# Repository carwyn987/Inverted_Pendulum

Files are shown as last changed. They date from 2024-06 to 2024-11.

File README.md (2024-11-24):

# Inverted-Pendulum Project

## What is an inverted pendulum?
An [inverted pendulum](https://en.wikipedia.org/wiki/Inverted_pendulum) is a dynamic system with the center of mass above its pivot point, generally constrained to one rotational degree of freedom. While a pendulum is stable, inverting a pendulum requires active balancing applied to it. Generally, this is performed by applying torque to the pendulum directly, or shifting the base longitudinally.

## History of Project

### Final TD3 Performance

https://github.com/user-attachments/assets/6cc0a676-86f2-4fd9-accb-2f986fe4a135

### Postsite / Retrospective Analysis

Reinforcement learning is ***INCREDIBLY CHALLENGING*** to transfer from simulation to reality - especially if you don't know the dynamics of the environment. 

The biggest difficulty was matching my simulation to the environment:
 - Most inverted pendulum simulations (CartPole-v1 from gymnasium) have force as the input quantity. My hardware used a stepper motor, with discrete choices for step sizes and timing. 
 - Due to the stepper motor, I also was constrained to a maximum speed.
 - The default parameters for the gymnasium environment do not seem to map to true dynamics. It seemed like my pendulum fell much faster than the simulation  rod.
 - Traditional methods such as PID control loops are well known for a reason - they work, are simple to set up. The only annoyance is tuning.

### Presite Updates

DQN Model balances pendulum, but cannot converge from hanging (stable) initialization in a reasonable amount of time and resources.

TD3 trained to convergence on episodes of length 1000 steps (0.02s resolution = 20s). Video below. Note: there are perturbations in the test, which explain some unexpected movements. These represent external forces acting on the pole, or noise in the system.

https://github.com/carwyn987/Inverted_Pendulum/assets/28845732/e16f0db4-fafe-4622-8498-058ad09bbe2e

Reward function that worked well for TD3:
```
reward = math.cos(theta % (2*math.pi)) + 1
if theta > -1 * math.pi/24 and theta < math.pi/24:
    reward += 10
if reward < 0: reward = 0
```
Note the lack of an explicit x-position component, which explains the full use of horizontal space by the agent.

### 2024

After a long intermission, I have decided to re-approach the project. However, I have an agenda in mind. As I will be traveling back to where the hardware is for one week only, I wish to simulate a solutions type of job, where the employee is dispatched to an on-site location, where they are responsible for quickly getting a system up and running. Therefore, I plan to prepare for this trip, and see how much I can minimize the on-site time necessary to get the pendulum balanced. Furthermore, I want to make the goals specific and as numerous as possible, so the goal is the following:

1. Enable the pendulum to balance "continuously". For testing purposes, I define this as "achieved" when the following test are completed successfully:
   - 5 individual tests, all 5 must pass first try with a unique codebase.
   - Sample an initial pendulum angle from vertical within the range of [-10,10] degrees.
   - Sample an initial longitudinal position within the middle 30% of the total range.
   - Set up the initial conditions by hand, and release contact with the pole as soon as movement is perceived after starting the program.
   - The pole must balance for 60 seconds for "success" to be achieved.
2. The same algorithm should enable the pole to swing up from a stationary position. I define this as "achieved" when the following test are completed successfully:
   - Begin with the pendulum stationary hanging at the lowest point (180 degrees from vertically upward (azimuth/heading/yaw(?)))
   - Execute the program, and without any contact from the tester, the pendulum should reach a balanced (varying <10 degrees from vertical over at least 10 seconds) within 30 seconds.
3. Just for funsies, a separate algorithm should enable the pendulum to make rotations of the pendulum. I define this as "achieved" when the following test are completed successfully:
   - Starting the test with the rod stationary in the downwards position, the rod should make >=10 full rotations in under 45 seconds.
4. Reach goal: if I achieve this, consider me a god (lowercase g). Modify the system somehow (make it visually based perhaps?) to enable a double pendulum to balance. This will involve hardware modifications to add another joint.

### 2018

In the naive implementation (2018), a deterministic model was created as a decision tree, with a few possible movements based from binning various encoder angles. It was during this year when the hardware component was constructed, and the results were presented in an independent research project class.

Unfortunately, the feedback loop was not responsive enough to maintain a balanced state, however the proof of concept was there.

During this phase, a few iterations of design were explored. Primarily, testing was performed on both a Raspberry PI and an Arguino Mega. There were moments of significant garbage collection, which justified use of the Arduino. Furthermore, the initial design of the hardware used a drawer slide and a servo, which was not an ideal combo due to the control of the servo, and the significant mass of the drawer slide, which contributed to a system with minimal ability to impart movement to the pendulum.

https://github.com/carwyn987/Inverted_Pendulum/assets/28845732/88b4a921-044d-4a91-877d-22acfd15797b

https://github.com/carwyn987/Inverted_Pendulum/assets/28845732/74fb59c1-3fed-446d-82f0-261624505b5c

These can also be viewed on [my youtube channel](https://www.youtube.com/channel/UCNOUx60VSDCHhShPJUi3yFg).

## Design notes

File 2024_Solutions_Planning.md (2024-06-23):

# Overview

Here I will plan the technical aspects to ensure readiness and success for on-site integration and testing.

# Review of Goals from README

1. Enable the pendulum to balance "continuously". For testing purposes, I define this as "achieved" when the following test are completed successfully:
   - 5 individual tests, all 5 must pass first try with a unique codebase.
   - Sample an initial pendulum angle from vertical within the range of [-10,10] degrees.
   - Sample an initial longitudinal position within the middle 30% of the total range.
   - Set up the initial conditions by hand, and release contact with the pole as soon as movement is perceived after starting the program.
   - The pole must balance for 60 seconds for "success" to be achieved.
2. The same algorithm should enable the pole to swing up from a stationary position. I define this as "achieved" when the following test are completed successfully:
   - Begin with the pendulum stationary hanging at the lowest point (180 degrees from vertically upward (azimuth/heading/yaw(?)))
   - Execute the program, and without any contact from the tester, the pendulum should reach a balanced (varying <10 degrees from vertical over at least 10 seconds) within 30 seconds.
3. Just for funsies, a separate algorithm should enable the pendulum to make rotations of the pendulum. I define this as "achieved" when the following test are completed successfully:
   - Starting the test with the rod stationary in the downwards position, the rod should make >=10 full rotations in under 45 seconds.
4. Reach goal: if I achieve this, consider me a god (lowercase g). Modify the system somehow (make it visually based perhaps?) to enable a double pendulum to balance. This will involve hardware modifications to add another joint.

# Brainstorming

## Design Questions
 - Will I run compute on the same machine as the control? 
   - If I train on my laptop, it may be easier to use an ethernet communication interface, simply using the arduino as an intermediary.
 - How will I train? Is there a sample and time efficient enough algorithm to run in real-time, or is pretraining necessary?
 - If I simulate the environment, how will I ensure generalization to real life? 
   - Should I parameterize on intrinsic properties, such as mass of rod, total longitudinal distance, and maximum movement speeds
   - Will training on all of these parameters be prohibited on my local machine (3080ti)?
 - Simulation environment?
   - Python Gym (now gymnasium)
   - Gazebo (use ROS)?
   - Unreal Engine?
 - How should I format separation of training and inference? Presumably have a real-time inference program, potentially in a faster language such as C++.
   - This implies saving of model weights and loading in C++. Are there C++ libraries for this? (PyTorch C++ API)

## Predicted Issues

 - The encoder readings may not translate to the trained-upon data.
   - Compute a mapping function given some benchmark with an expectation (pendulum oscillations under gravity). Furthermore, it may be an interesting idea to use benchmarks like this as parameters (time for the pendulum to come to a stop given a 30 degree initialized unassisted swing (aka representation of system friction) - may differ if platform can and can't move).
 - The response of a given control signal will vary, in moments as well as duration, magnitude, and oscillatory behavior. 
   - Similar approach to encoder using a mapping. Perhaps also run some tests to see if we can replicate our trained-upon data?
 - Similar to my prior attempts, there will be an issue with the fact that I am currently dead-reckoning longitudinal position.

## Ideas

 - Redesign to use a camera for inputs
   - This will remove the need to use an encoder, and allow for determination of longitudinal displacement. Furthermore, it will allow me to try a double pendulum regardless of not having another encoder.
   - However, it will be challenging to ensure generalization. I may need to simulate the environment with a variety of backgrounds, and a particularly colored rod for this to work well. I could also use a colored sheet as the background, but that feels like cheating.
 - Set up a cloud-based GPU training device that can take an image of the environment. This will allow significant speed-ups due to larger batch sizes, and data and model parallelism capability. Therefore, it will be more realistic to retrain within an hour or two. That being said, in my experience, it's unlikely (if the code is not buggy) a task like this will require more than 24 hours of training, which is technically doable locally in the time frame allotted.
 - Modularize the system. Have a few interchangeable components for each module. An example of this would be having a module reponsible for determining the absolute angle of the pendulum. Then, I can build an image-based solution, an encoder-based solution, a naive and model-based approach for both, etc, and trade out these components to get it working.
   - I like this modular idea, because it allows me to continue progressing on this until the day I leave, without ever leaving much work unfinished.

## Advice

 - List out all unknowns.
 - Don't overparametrize model. If modularization is performed, use best guesses for other dynamics and values.
 - Know what tools I am familiar with, what they can do, and plan out every tool I will use.

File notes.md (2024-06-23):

# 06/23/24 Status Update

## Accomplishments thus far

TD3 Trained well locally in ~1 hour to swing up and balance pendulum.
Received part numbers of encoder and stepper motor components - need to write interfaces for those components.
 - Let me diagram out a system schematic so that I can code up interplay of components and draft specifics.

Sensitivity analysis complete.
 - Latency up to 4ms is handled by existing model without much loss in performance.
 - Maximum x threshold distance has huge impacts on performance, luckily our estimate should be realatively accurate, and we can simply add a scaling factor to compensate.
 - By far the most impactful parameter on evaluation performance is the rod length. This was expected, as the moment of inertia of a rod about its end is $I=\frac{1}{3}ML^{2}$ - though this doesn't match my intuition that mass would be the most impactful parameter. In fact, length is so important, halving or doubling it in our environment causes the model to fail to swing the rod up at all. Therefore, I will need to parameterize my model on this.

As one of my goals is for the swung-up rod to maintain a centered position in the x-axis, I also need to add reward for staying centered. This should improve robustness, as small perturbations, or failure to correctly estimate x position, will be less likely to push the cart into the stops at each end of the track.

I also have a good idea of the parameter size necessary for a policy to approximate swing-up and balance behavior. In the DQN, the model consisted of:
```
Action_Value_Network(
  (fc1): Linear(in_features=4, out_features=64, bias=True)
  (fc2): Linear(in_features=64, out_features=64, bias=True)
  (fc3): Linear(in_features=64, out_features=64, bias=True)
  (fc4): Linear(in_features=64, out_features=21, bias=True)
)
----------------------------------------------------------------
        Layer (type)               Output Shape         Param #
================================================================
            Linear-1                   [-1, 64]             320
            Linear-2                   [-1, 64]           4,160
            Linear-3                   [-1, 64]           4,160
            Linear-4                   [-1, 21]           1,365
================================================================
Total params: 10,005
Trainable params: 10,005
Non-trainable params: 0
----------------------------------------------------------------
Input size (MB): 0.00
Forward/backward pass size (MB): 0.00
Params size (MB): 0.04
Estimated Total Size (MB): 0.04
```

In TD3, we have:
```
Actor(
  (l1): Linear(in_features=4, out_features=256, bias=True)
  (l2): Linear(in_features=256, out_features=256, bias=True)
  (l3): Linear(in_features=256, out_features=1, bias=True)
)
Critic(
  (l1): Linear(in_features=5, out_features=256, bias=True)
  (l2): Linear(in_features=256, out_features=256, bias=True)
  (l3): Linear(in_features=256, out_features=1, bias=True)
  (l4): Linear(in_features=5, out_features=256, bias=True)
  (l5): Linear(in_features=256, out_features=256, bias=True)
  (l6): Linear(in_features=256, out_features=1, bias=True)
)
----------------------------------------------------------------
        Layer (type)               Output Shape         Param #
================================================================
            Linear-1                  [-1, 256]           1,280
            Linear-2                  [-1, 256]          65,792
            Linear-3                    [-1, 1]             257
================================================================
Total params: 67,329
Trainable params: 67,329
Non-trainable params: 0
----------------------------------------------------------------
Input size (MB): 0.00
Forward/backward pass size (MB): 0.00
Params size (MB): 0.26
Estimated Total Size (MB): 0.26
----------------------------------------------------------------
```

## What now?

 - Train another model on +1 parameter. As training time is almost certainly positively correlated with number of input parameters, and likely has a power law or exponential relationship, this should be setup on a cloud provider to enable scalability and speedups.
   - Currently using Gymnasium classic_control environment (not MuJoCo, Gazebo, or any other simulator / physics engine). Probably easiest to stick with this, but if time enables, I should try replicating environment, training, and simulation with Gazebo on AWS RoboMaker.
 - Review old code, diagram the system design, write adapters for encoder and stepper (alternatively, since I'm training another model, write environment adapters to simulate encoder readings, and to use stepper motor impulses to control to encapsulate the intermediate step in DNN for real-time execution).
 - I will also need to write a state estimation algorithm that maintains current estimates of x, theta, and derivatives for inference.
 - Remember to modularize (i.e. focus on communication medium and packet descriptions first) for ease of algorithm modifications.

## Notes on encoder and stepper motor

It definitely looks like I used a stepper driver in the initial design, but I can't make out which driver it is. This will have to wait until I'm on-site to develop further.

Almost all stepper drivers support **microstepping** between 1/8th and 1/256th.
Stepper motor specs:
 - 8.6V
 - 1A / coil
 - 200 steps / revolution = 1.8 degrees / step
 - Holding torque of 14 kg-cm

Encoder specs:
 - 2000 P/R = 0.18 degrees / "step"

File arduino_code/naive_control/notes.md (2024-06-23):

This Arduino code is designed to balance an inverted pendulum using a stepper motor and feedback from an incremental rotary encoder and two limit switches. Here's a breakdown of the code:
Includes and Definitions

    The code includes the Streaming library for serial communication.
    Defines constants for pins connected to the encoder, limit switches, and stepper motor.
    Defines a struct stepSizeAndDir to represent the stepper motor's step size and direction.
    Defines a variable count to store the encoder's count value.

Setup

    Sets up the pins as inputs or outputs using pinMode and DDR registers.
    Enables internal pull-up resistors for the limit switch pins.
    Attaches interrupts to the encoder pins (ISR_FOR_ENCODER_B and ISR_FOR_ENCODER_A) and limit switch pins.
    Initializes serial communication at 250000 baud.

Loop

    Checks if the serial buffer has changed and returns if it has.
    Reads the current encoder count value and stores it in rncount.
    Disables interrupts (cli) and reads the current count value.
    Enables interrupts (sei) and calculates the stepper motor's step size based on the encoder value.
    Sets the stepper motor's direction and step size using the PORTA register.
    Steps the stepper motor using the PORTA register and delay functions.

Interrupt Service Routines (ISRs)

    isrA and isrB are called when the encoder pins change state. They update the count variable based on the encoder's phase A and phase B values.
    isrLimit is called when a limit switch is triggered, setting the atLimit flag to true.

Stepper Motor Control

    The stepper motor is controlled using the PORTA register, which sets the step size and direction.
    The stepper motor is stepped using the PORTA register and delay functions.

Encoder Value Calculation

    The encoder value is calculated based on the count variable and used to determine the stepper motor's step size.

Limit Switch Handling

    When a limit switch is triggered, the atLimit flag is set to true, and the code exits the loop.

Overall, this code uses a combination of encoder feedback and limit switches to balance an inverted pendulum using a stepper motor.

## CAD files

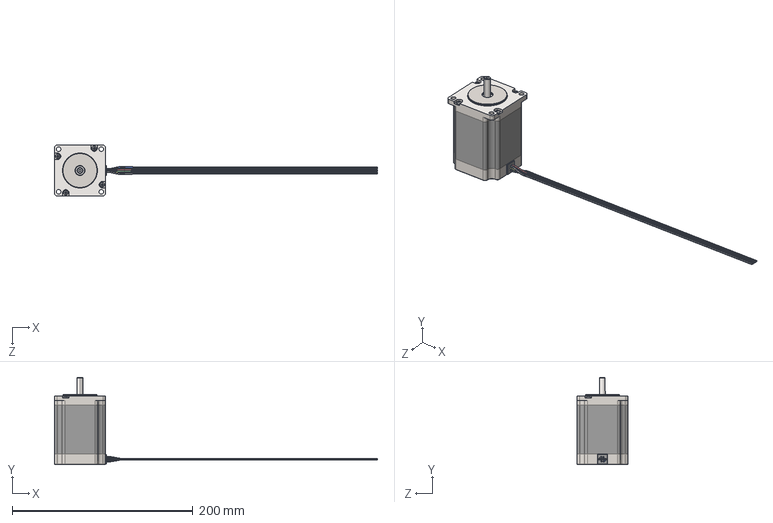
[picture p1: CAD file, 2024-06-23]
Documents/stepper/SY57STH76-1006A.step
357.4 x 96.6 x 56.4 mm

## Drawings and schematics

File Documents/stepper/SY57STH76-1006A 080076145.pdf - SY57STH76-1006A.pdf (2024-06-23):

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

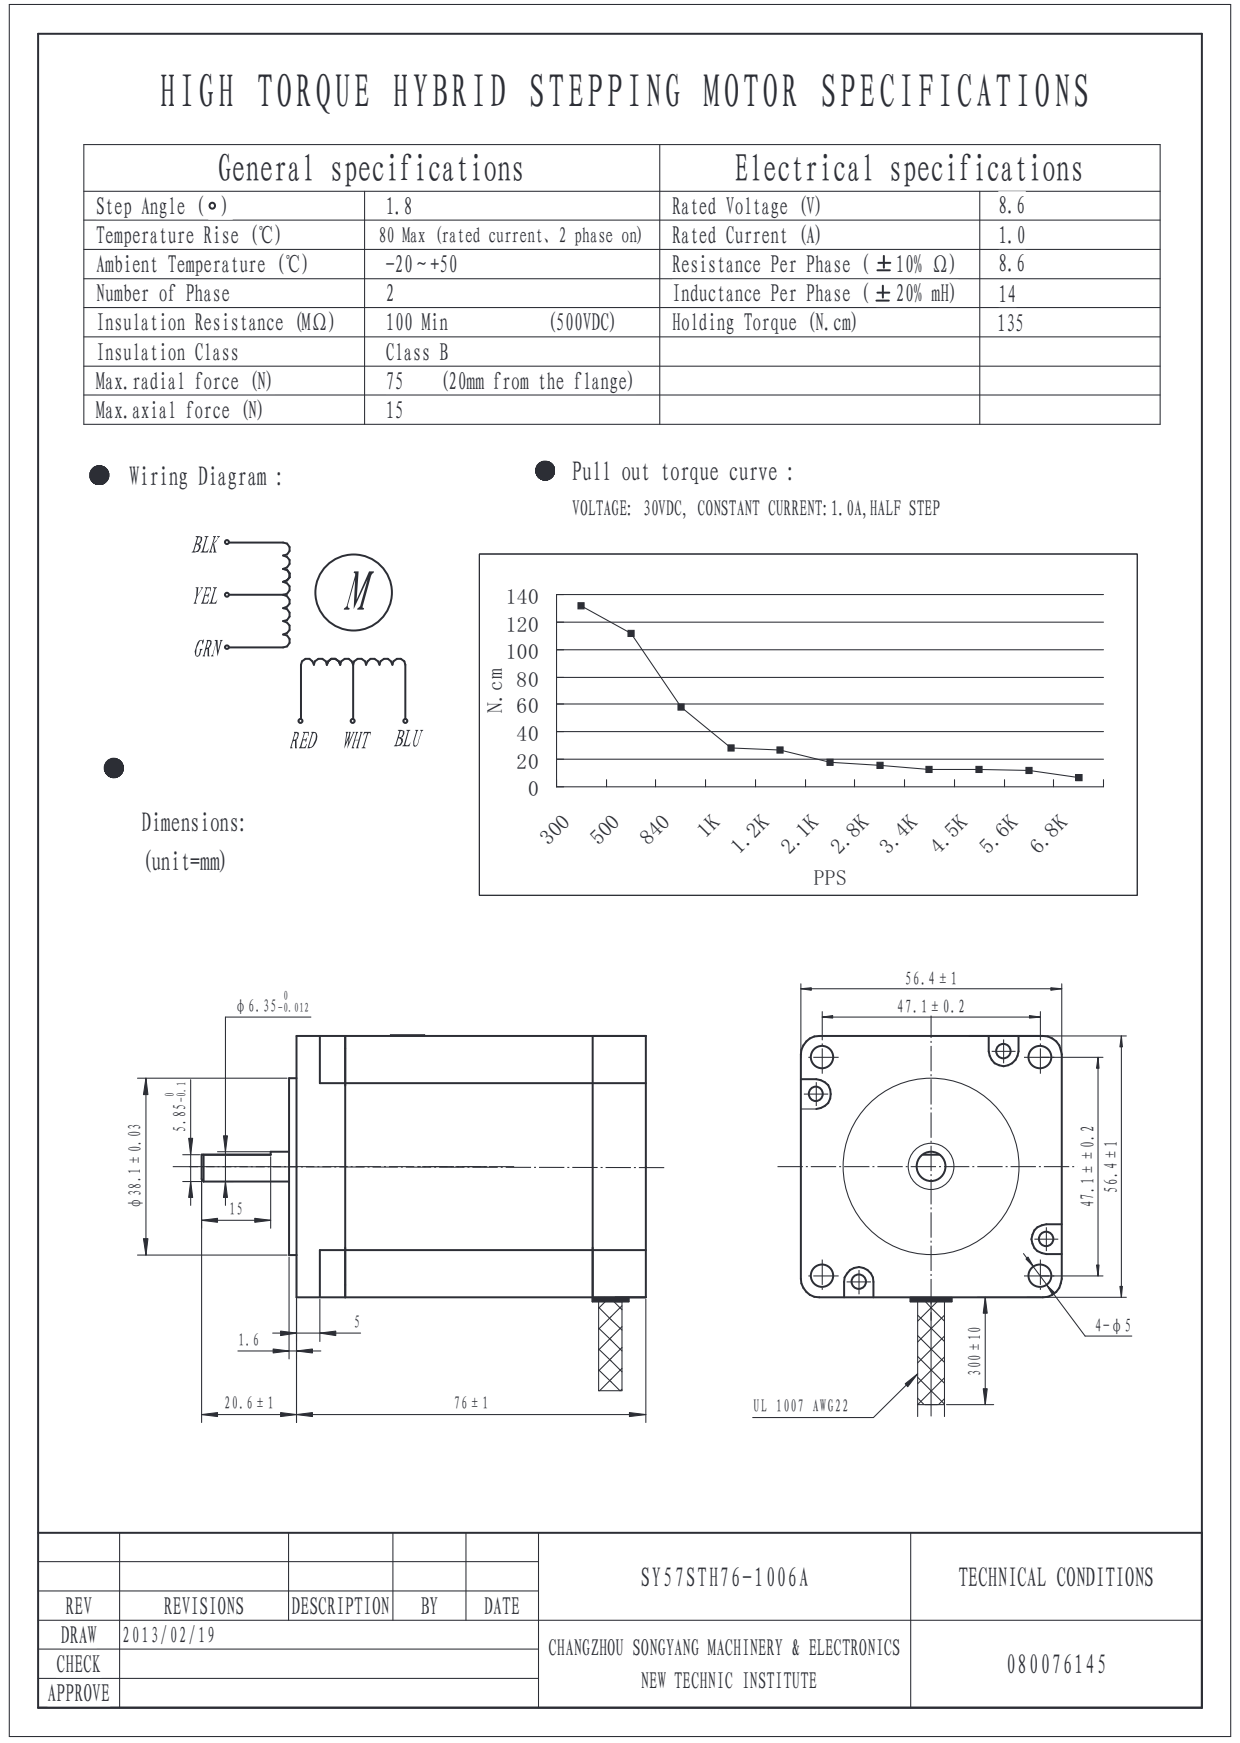
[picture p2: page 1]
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

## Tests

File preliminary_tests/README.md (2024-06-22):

Environment
 - Inverted Pendulum Simulation
 - Observation space: (x,xdot,theta,thetadot)
 - Variable force application, [-1,1]
 - Random variations in initialization positions, velocities, and angular equivalents
 - Random perturbations

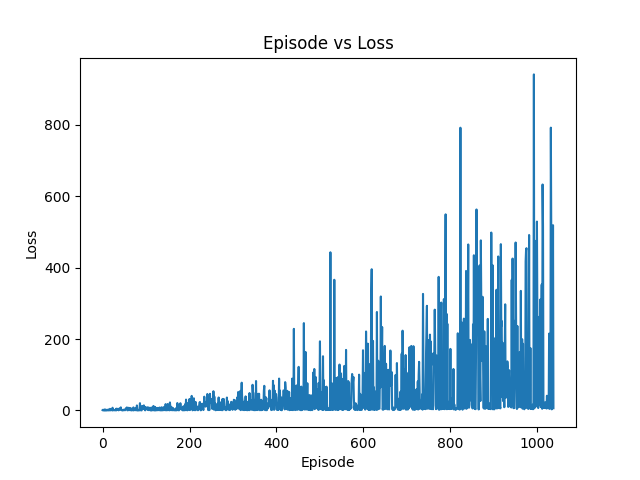
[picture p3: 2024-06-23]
preliminary_tests/media/init_pendulum_down/episode_loss_plot.png

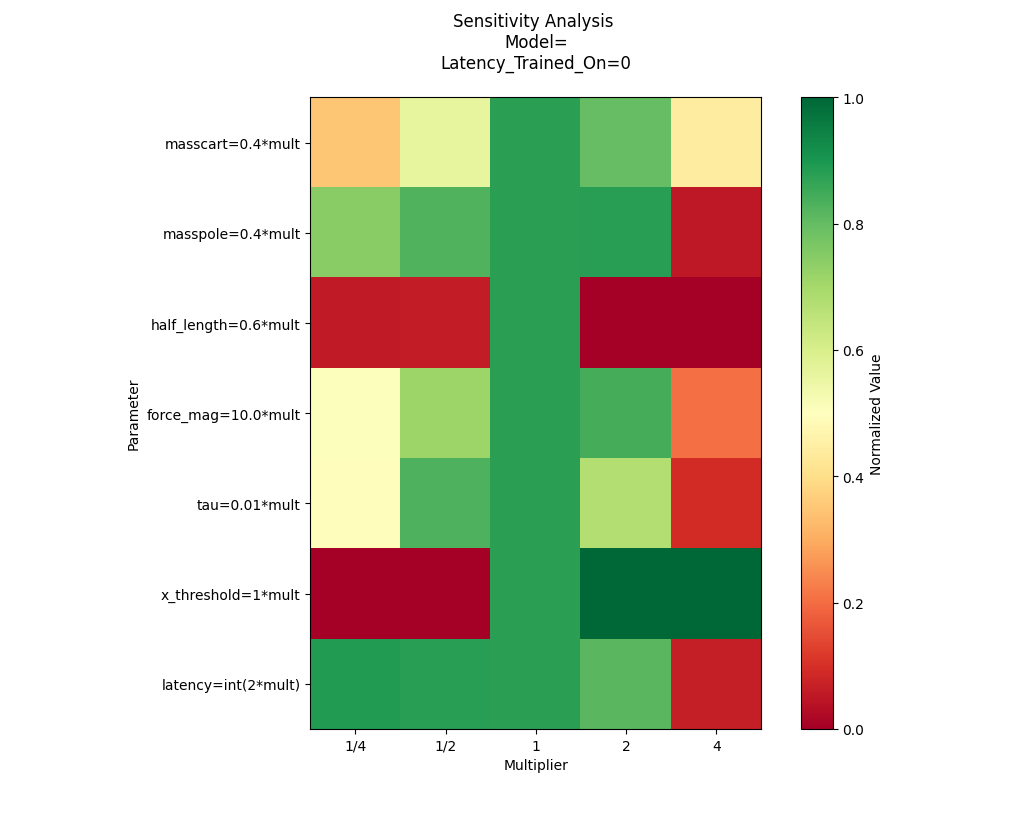
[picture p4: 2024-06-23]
preliminary_tests/media/td3_swing_up_and_balance_sensitivity_analysis.png

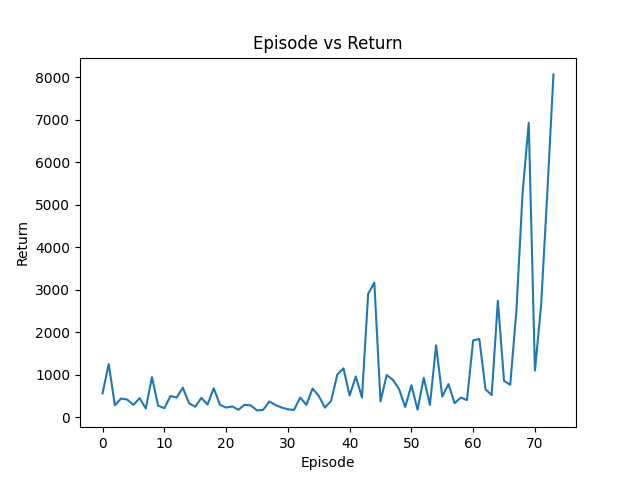
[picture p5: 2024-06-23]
preliminary_tests/media/init_pendulum_down/episode_return_theoretical_max_shy_of_10000.png

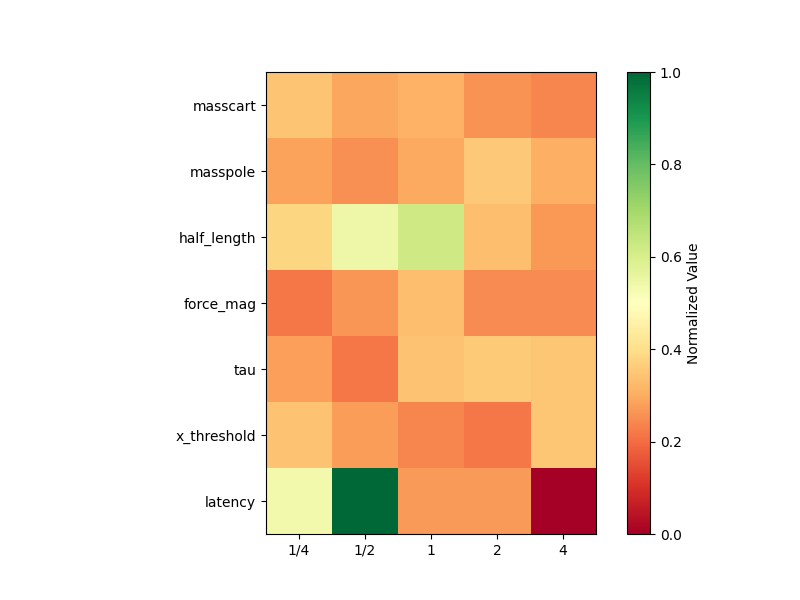
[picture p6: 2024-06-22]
preliminary_tests/media/init_pendulum_up/sensitivity_latency_2_on_min_perturb_model.png

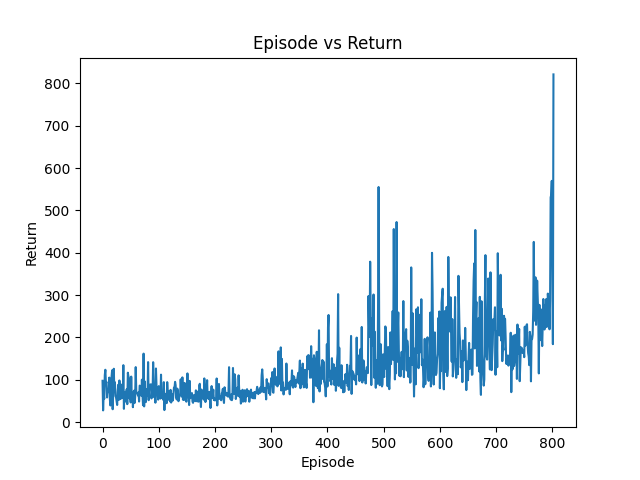
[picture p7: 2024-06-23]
preliminary_tests/media/init_pendulum_down/episode_return_plot.png

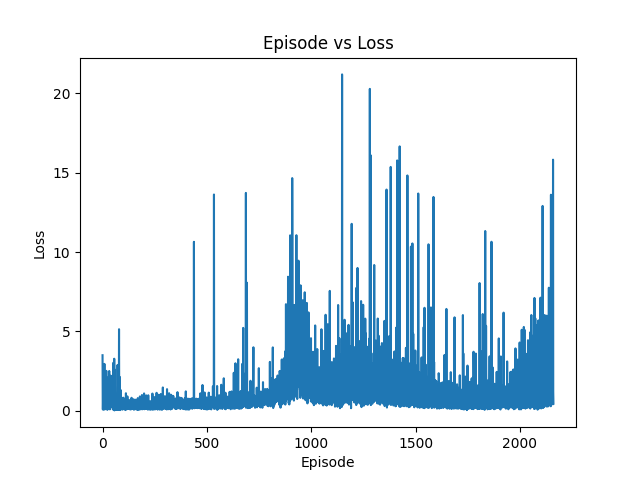
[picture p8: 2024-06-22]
preliminary_tests/media/init_pendulum_up/best_minimal_perturbations_episode_loss_plot.png

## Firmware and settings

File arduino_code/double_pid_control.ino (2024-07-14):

#include <Streaming.h>

int serialAv; // Variable to store the serial availability

//Stepper motor pins
const int dirPin = 25;
const int steppin = 26;
const int mOPin = 22;
const int mlPin = 23;
const int m2Pin = 24;

//limit switch pins
const int leftLimitPin = 15;
const int rightLimitPin = 18;

// Define constants for encoder ISR pins
const int ISR_FOR_ENCODER_B = 20; // Pin for encoder ISR B
const int A = 21; // Pin for encoder phase A
const int Z = 19; // Pin for encoder phase Z (index)

// Define variables for encoder count
volatile int16_t count = -4000; // Variable to store encoder count
int lastCount = -2000; // Variable to store previous encoder count

float pos = 0.0;
int left_to_right = 0;

// Limit Switch variable
bool atLimit = false;
bool prevAtLimit = false;

// uint8_t stepSize AndDir = B00000000; //00000001 is m0, 00000010 is ml, 00000100 is m2, 00001000 is dir.
unsigned int stepPulseWidth = 2600; //in milliseconds

unsigned long start_ts = millis() / 1000;

void setup() {
  DDRD = B11111000; // Direction register for Port A (some range of arduino digital pins); 0 = input, 1 = output...
  DDRA = B11111111; // sets PAO PA4 (step, dir, m0, ml, m2) to Outputs
  PORTA = B00000000; // Set all pins on Port A to low
  
  // Encoder direction
  pinMode(A, INPUT);
  pinMode(Z, INPUT);
  pinMode(ISR_FOR_ENCODER_B, INPUT);

  // Limit switch direction
  pinMode(leftLimitPin, INPUT);
  pinMode(rightLimitPin, INPUT);

  // Encoder pullup resistor
  digitalWrite(A, HIGH);
  digitalWrite(ISR_FOR_ENCODER_B, HIGH);
  digitalWrite(Z, HIGH); // Set encoder phase Z (index) pin high

  // limit switch pullup resistor
  digitalWrite(leftLimitPin, HIGH);
  digitalWrite(rightLimitPin, HIGH);

  PORTA &= B00000000; // Clear Port A (some range of Arduino digital pins)

  // Attach interrupts for encoder
  attachInterrupt(digitalPinToInterrupt(ISR_FOR_ENCODER_B), isrB, CHANGE);
  attachInterrupt(digitalPinToInterrupt(A), isrA, CHANGE);

  // Attach interrupts for limit switches
  attachInterrupt(digitalPinToInterrupt(leftLimitPin), isrLimit, CHANGE);
  attachInterrupt(digitalPinToInterrupt(rightLimitPin), isrLimit, CHANGE);
  
  Serial.begin(115200);
  // Serial.println("Press a key to begin execution ...");
  // while ((serialAv = Serial.available()) == 0) { } // Wait for first serial input
  calibrate(5000);
}

bool alwaysExit = false;

void loop() {
  // if (digitalRead(rightLimitPin)) {
  //   for (int i = 0; i<left_to_right/2; i++){
  //     step_stepper_motor(-1.0, stepPulseWidth, true);  
  //   }
  //   atLimit = false;
  // }
  // if (digitalRead(leftLimitPin)){
  //   for (int i = 0; i<left_to_right/2; i++){
  //     step_stepper_motor(1.0, stepPulseWidth, true);  
  //   }
  //   atLimit = false;
  // }
  // if ((digitalRead(rightLimitPin) && prevAtLimit) || (digitalRead(leftLimitPin) && prevAtLimit) || (atLimit && prevAtLimit)){
  //   return;
  // }
  if (alwaysExit) {
    return;
  }
  if (atLimit || digitalRead(rightLimitPin) || digitalRead(leftLimitPin)){
    delayMicroseconds(1000);
    if (digitalRead(rightLimitPin) || digitalRead(leftLimitPin)){
      alwaysExit = true;
      return;
    }else{
      atLimit = false;
    }
  }


  cli(); // Disable interrupts
  int16_t rncount = count; // Read encoder count
  sei(); // Enable interrupts

  // Send encoder value to computer
  Serial.print("a");
  Serial.println(rncount);
  
  // Read in the desired movement from the computer
  if (Serial.available() > 0) {
    float move_x = read_float_from_serial();
    float move = move_x; // / (2 * 3.14 * 0.028 * 1.8 / 360.0); // ~num steps

    // Move the stepper motor
    step_stepper_motor(move, stepPulseWidth, false);
  }
}

float read_float_from_serial() {
  String input = "";
  char incomingByte;
  while (Serial.available() > 0) {
    incomingByte = Serial.read();
    if (incomingByte == '\n') {
      break;
    }
    input += incomingByte;
  }
  return input.toFloat();
}

void isrA() {
    // Interrupt service routine for encoder phase A
    byte a = (PIND & B00000011);
    if (a & B00000001 == 1){ // If pin 0 (phase A) goes from low to high
        if (a == B00000000 || a == B00000011){
            --count;
        }else{
            ++count;
        }
    }else{ // Phase A goes from high to low
        if (a == B00000000 || a == B00000011){
            --count;
        }else{
            ++count;
        }
    }
    // Handle overflow and underflow of encoder count
    if (count < -4000) {
        count += 8000;
    } else if (count > 3999) {
        count -= 8000;
    }
}

void isrB() {
    // Interrupt service routine for encoder phase B
    byte b = (PIND & B00000011);
    if(b & B00000010 == 1){ // If pin 0 (phase B) goes from low to high
        if (b == B00000000 || b == B00000011){
            ++count;
        }else{
            --count;
        }
    }else{ // Phase B goes from high to low
        if (b == B00000000 || b == B00000011){
            ++count;
        }else{
            --count;
        }
    }
    // Handle overflow and underflow of encoder count
    if (count < -4000){
        count += 8000;
    } else if (count > 3999) {
        count -= 8000;
    }
}

void isrLimit() {
  atLimit = true;
}


// called during
void step_stepper_motor(float move, int numDelayMicroseconds, bool override_limit) {
  /*
  Assuming positive for clockwise and negative for counter-clockwise, takes a float representing the movement desired
  by the stepper motor, takes a step.
  */

  // Reset step options
  PORTA &= B11111000;

  int direction = 0;

  // Set the direction of the stepper motor
  if (move > 0){
    PORTA |= B00001000; // Set the direction pin high
    direction = 1;
  }else{
    PORTA &= B11110111; // Set the direction pin low
    direction = -1;
  }
  move = abs(move);

  float applied_movement = 0.0;

  // Set the step size
  // step size choices: {1.0/32.0, 1.0/16.0, 1.0/8.0, 1.0/4.0, 1.0/2.0, 1.0}
  // float cutoffs[] = {1.0, 0.75, 0.375, 0.1875, 0.09375, 0.046875, 0.03125}; // These are the midpoints between step sizes
  float cutoffs[] = {999999, 1.0, 0.8, 0.6, 0.4, 0.2, 0.2, 0.0};
  
  int indx = 0;
  for (int i = 0; i < 7; i++){
    if (move < cutoffs[i] && move >= cutoffs[i+1]){
      indx = i;
      break;
    }
  }

  // Binary Step Repr.: 000  100   010   110  001    111 or 011  101
  // Actual Step Size:  1    1/2   1/4   1/8  1/16   1/32
  switch (indx) { //SETS STEP SIZE
    case 0: //MAX STEP
      applied_movement = 1.0;
      break;
    case 1:
      PORTA |= B00000001;
      applied_movement = 1.0/2.0;
      break;
    case 2:
      PORTA |= B00000010;
      applied_movement = 1.0/4.0;
      break;
    case 3:
      PORTA |= B00000011;
      applied_movement = 1.0/8.0;
      break;
    case 4:
      PORTA |= B00000100;
      applied_movement = 1.0/16.0;
      break;
    case 5:
      PORTA |= B00000110;
      applied_movement = 1.0/32.0;
      break;
    case 6:
      PORTA |= B00000110;
      applied_movement = 1.0/32.0;
    default:
      PORTA |= B00000110;
      applied_movement = 1.0/32.0;
  }

  // PORTA |= B00000000; // 0.75
  // PORTA |= B00000001; // 1.5
  // PORTA |= B00000010; // 3
  // PORTA |= B00000011; // 6
  // PORTA |= B00000100; // 12
  // PORTA |= B00000110; // 26

  pos += direction * applied_movement * 1.8 * 2 * 3.14159 * 0.028 / 360;
  Serial.print("x");
  Serial.println(pos);

  if(!atLimit || override_limit){
    // Set the step pin high
    PORTA |= B00010000;
    delayMicroseconds(numDelayMicroseconds);
    PORTA &= B11101111;
    delayMicroseconds(numDelayMicroseconds/4); 
  }
}

int move(int step, int limitPin){
  
  bool last_limit_reached = false;
  int count_steps = 0;
  
  // move
  while (!atLimit && !(digitalRead(limitPin) == HIGH && last_limit_reached)){
    step_stepper_motor(step, stepPulseWidth, false);
    
    if(!atLimit){
      count_steps += 1;
    }
    if(digitalRead(limitPin) == HIGH){
      last_limit_reached = true;
    }
  }

  return count_steps;
}

void calibrate(float step_time){

  // set time
  float save_step_time = stepPulseWidth;
  stepPulseWidth = step_time;
  
  int count_steps = 0;

  float stepsize_tmp = 1.0;

  // move right
  count_steps = move(stepsize_tmp, rightLimitPin);

  int backup_from_limit = 20;
  int left_steps = count_steps - backup_from_limit;
  // Serial.print("Steps from start to left = ");
  // Serial.println(left_steps);
  count_steps = 0;

  // backup
  for (int i = 0; i < backup_from_limit; i++){
    step_stepper_motor(-1 * stepsize_tmp, stepPulseWidth, true); // move off limit switch
  }
  atLimit = false;

  // move left
  count_steps = move(-1.0 * stepsize_tmp, leftLimitPin);

  left_to_right = count_steps - backup_from_limit;
  // Serial.print("Steps from left to right = ");
  // Serial.println(left_to_right);

  // backup
  for (int i = 0; i < backup_from_limit; i++){
    step_stepper_motor(stepsize_tmp, stepPulseWidth, true); // move off limit switch
  }
  atLimit = false;

  // move to the center
  for (int i = 0; i<int(1.35 * left_to_right/2); i++){
    step_stepper_motor(stepsize_tmp, stepPulseWidth, true);  
  }
  
  pos = 0;
  atLimit = false;

  stepPulseWidth = save_step_time;
}

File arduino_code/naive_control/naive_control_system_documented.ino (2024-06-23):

/*
Stepper Motor:
https://www.pololu.com/product/1477/faqs
Pololu Stepper Motor: Unipolar/Bipolar, 200 Steps/Rev, 57×76mm, 8.6V, 1 A/Phase Item 1477 SOYO

Likely Drivers:
https://www.pololu.com/category/120/stepper-motor-drivers
https://www.pololu.com/category/212/tic-stepper-motor-controllers 

Encoder:
https://www.ia.omron.com/product/item/2463/

*/

#include <Streaming.h> // Include the Streaming library for serial communication

// Define global variables
int serialAv; // Variable to store the serial availability

// Define constants for encoder ISR pins
const int ISR_FOR_ENCODER_B = 20; // Pin for encoder ISR B
const int A = 21; // Pin for encoder phase A
const int Z = 19; // Pin for encoder phase Z (index)

// Define constants for limit switch pins
const int leftLimitPin = 18; // Pin for left limit switch
const int rightLimitPin = 19; // Pin for right limit switch

// Define constants for stepper motor pins
const int dirPin = 25; // Pin for stepper motor direction
const int steppin = 26; // Pin for stepper motor step
const int mOPin = 22; // Pin for stepper motor microstep 0
const int mlPin = 23; // Pin for stepper motor microstep 1
const int m2Pin = 24; // Pin for stepper motor microstep 2

// Define variables for stepper motor control
uint8_t stepSizeAndDir = B00000000; // Variable to store step size and direction
unsigned long stepPulseWidth = 2; // Variable to store step pulse width in milliseconds

// Define variables for encoder count and limit switch state
volatile int16_t count = -2000; // Variable to store encoder count
bool atLimit = false; // Variable to store limit switch state

int lastCount = -2000; // Variable to store previous encoder count

void setup() {
    // Set up pins as inputs or outputs
    DDRD &= B11111000; // Set direction register for Port D (some range of Arduino digital pins) to input
    DDRA = B11111111; // Set direction register for Port A (some range of Arduino digital pins) to output

    pinMode(leftLimitPin, INPUT);
    pinMode(rightLimitPin, INPUT);

    // Writing HIGH to INPUT pins enables the internal pull-up resistor!
    digitalWrite(leftLimitPin, HIGH);
    digitalWrite(rightLimitPin, HIGH);

    digitalWrite(A, HIGH);
    digitalWrite(ISR_FOR_ENCODER_B, HIGH);
    digitalWrite(Z, HIGH); // Set encoder phase Z (index) pin high

    PORTA &= B00000000; // Clear Port A (some range of Arduino digital pins)

    digitalWrite(26, LOW); // Set stepper motor step pin low

    // Attach interrupts for encoder and limit switches
    attachInterrupt(digitalPinToInterrupt(ISR_FOR_ENCODER_B), isrB, CHANGE);
    attachInterrupt(digitalPinToInterrupt(A), isrA, CHANGE);
    attachInterrupt(digitalPinToInterrupt(leftLimitPin), isrLimit, CHANGE);
    attachInterrupt(digitalPinToInterrupt(rightLimitPin), isrLimit, CHANGE);

    Serial.begin(250000); // Initialize serial communication at 250000 baud
    Serial.println("hi"); // Print "hi" to serial monitor

    while ((serialAv = Serial.available()) == 0) { } // Wait for serial data to be available
}

void loop() {
    // Check if serial data is available
    if (Serial.available() != serialAv) {
        return;
    }

    // Check if limit switch is triggered
    if (atLimit) {
        return;
    }

    // Disable interrupts
    cli();

    // Read encoder count
    int16_t rncount = count;

    // Enable interrupts
    sei();

    // Calculate encoder value based on count
    uint8_t encodVal = 6;
    if (rncount >= 6) {
        encodVal = 12;
    } else if (rncount <= -6) {
        encodVal = 0;
    } else {
        encodVal += rncount;
    }

    // Set stepper motor step size and direction based on encoder value
    PORTA &= B11111000;
    switch (encodVal) {
    case 6:
        return;
    case 5:
    case 7:
        PORTA |= B00000101;
        break;
    case 4:
    case 8:
        PORTA |= B00000100;
        break;
    case 3:
    case 9:
        PORTA |= B00000011;
        break;
    case 2:
    case 10:
        PORTA |= B00000010;
        break;
    case 1:
    case 11:
        PORTA |= B00000001;
        break;
    case 0:
    case 12:
        PORTA |= B00000001;
        //PORTA |=B00000000;
        break;
    }

    // Set stepper motor direction based on encoder value
    if (encodVal > 6){
        PORTA |= B00001000;
    }else{
        PORTA &= B11110111;
    }

    // Step the stepper motor
    PORTA |= B00010000;
    delay(stepPulseWidth);
    PORTA &= B11101111;
    delay(stepPulseWidth);
}

/*
The isrA() and isrB() functions are called whenever there is a change in the state of 
the encoder phases A and B, respectively. They update the encoder count based on the 
direction of the change.

Based on https://www.youtube.com/watch?v=_YI_UJ910UY
I can probably replace some of the logic here by specifying RISING or FALLING in the 
attachInterrupt() function, and creating simpler ISR functions.
*/

void isrA() {
    // Interrupt service routine for encoder phase A
    byte a = (PIND & B00000011);
    if (a & B00000001 == 1){ // If pin 0 (phase A) goes from low to high
        if (a == B00000000 || a == B00000011){
            --count;
        }else{
            ++count;
        }
    }else{ // Phase A goes from high to low
        if (a == B00000000 || a == B00000011){
            --count;
        }else{
            ++count;
        }
    }
    // Handle overflow and underflow of encoder count
    if (count < -2000) {
        count += 4000;
    } else if (count > 1999) {
        count -= 4000;
    }
}

void isrB() {
    // Interrupt service routine for encoder phase B
    byte b = (PIND & B00000011);
    if(b & B00000010 == 1){ // If pin 0 (phase B) goes from low to high
        if (b == B00000000 || b == B00000011){
            ++count;
        }else{
            --count;
        }
    }else{ // Phase B goes from high to low
        if (b == B00000000 || b == B00000011){
            ++count;
        }else{
            --count;
        }
    }
    // Handle overflow and underflow of encoder count
    if (count < -2000){
        count += 4000;
    } else if (count > 1999) {
        count -= 4000;
    }
}

/*
The isrLimit() function is called whenever a limit switch is triggered. It sets the 
atLimit variable to true, indicating that the system has reached a limit.
*/

void isrLimit() {
    // Interrupt service routine for limit switches
    atLimit = true;
}

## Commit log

2024-06-23 Planning & analysis of sensitivity results.
    [SY57STH76-1006A.step]
2024-06-24 Began structuring ROS2 Humble package ... basic design of simulated encoder and start of state estimator.
2024-06-24 Figured out header file imports in ROS/CMake, full_state_estimator file nearly done, now need to work on savitzky-golay interpolation, or some other form of interpolation for state estimation. Probab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
    [simulated_encoder.cpp, state_estimator.cpp]
2024-06-28 Removed execution of socket code (it wasn't working right), and preparing to rebuild.
2024-06-28 Force-based simulation complete. Planning to revamp sim to more accurately map to stepper movement (as opposed to forces).
2024-07-01 arduino code tests working
2024-07-01 Serial comunication with encoder on arduino.
2024-07-04 Updates ... specifically to arduino code (limit switch debouncing) + calibration + real-time control with ROS + arduino + libtorch.
2024-07-05 Remote control - shows lack of power necessary to swing up pole.
2024-07-05 Swinging now works, but lacks power or precision input needed to swing all the way up. Needs a better model. Currently, model depends on time series input flattened to estimate velocity and theta-dot.
2024-07-10 Finally got rod swinging up and balancing with PID.
